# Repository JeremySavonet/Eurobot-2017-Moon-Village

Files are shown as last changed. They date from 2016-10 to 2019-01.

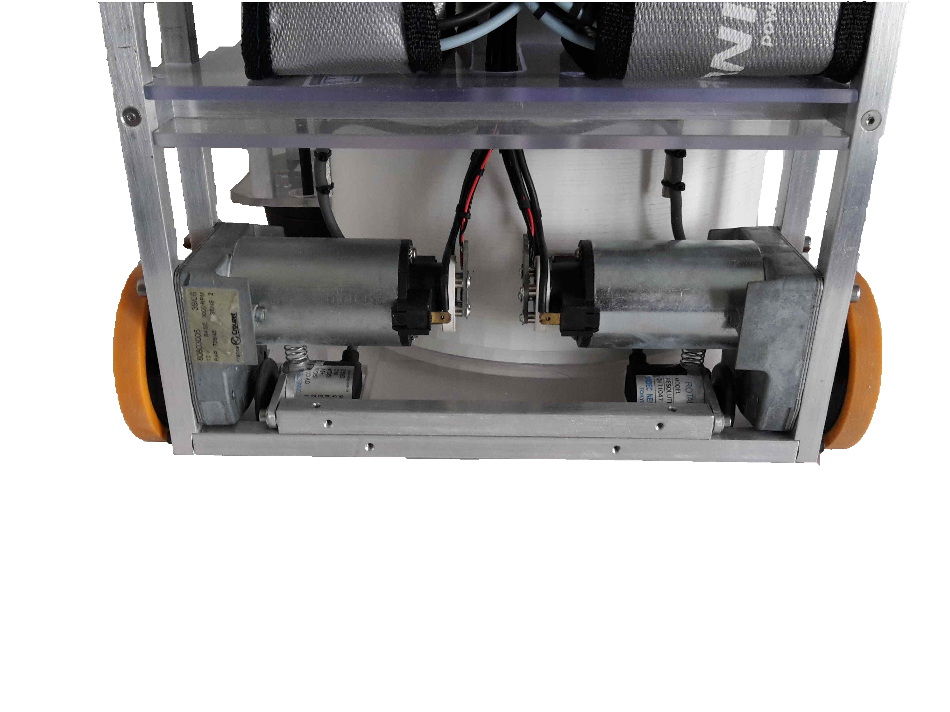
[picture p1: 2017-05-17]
admin/Poster/IMG_20170425_171114.png

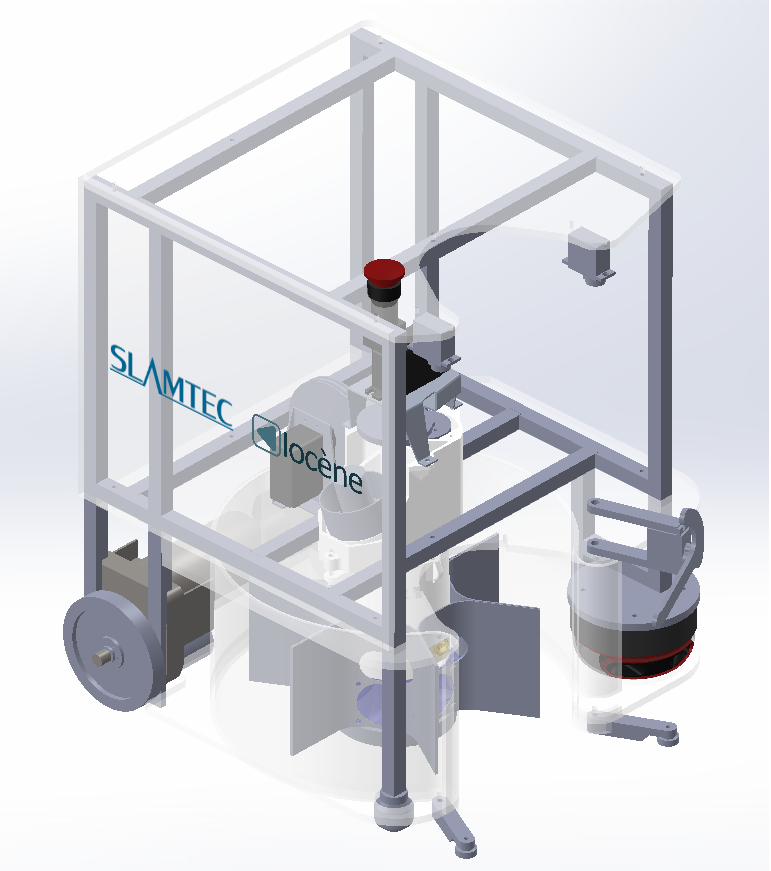
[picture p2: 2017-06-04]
meca/Images/Robot 1.png

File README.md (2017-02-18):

EUROBOT 2017 - Moon Village
====

Make the SD card with the Linux Image:
===

First checkout this repository by using:

```
shell$ git clone git://github.com/ikwzm/FPGA-SoC-Linux
shell$ cd FPGA-SoC-Linux
shell$ git lfs pull origin master
```

Make sure you have git lfs installed before running the third command.
If not installed, just type:
```
### On Debian:

echo 'deb http://http.debian.net/debian wheezy-backports main' > /etc/apt/sources.list.d/wheezy-backports-main.list
curl -s https://packagecloud.io/install/repositories/github/git-lfs/script.deb.sh | sudo bash
sudo apt-get install git-lfs
git lfs install

### On MacOs:
brew install git-lfs
git lfs install
```

When you are done, create the SD card. You will need to create two partition on it:
  * One around 524Mo in FAT format
  * The other around 2,7Go in Ext3 format

You can use the method of your choice to create those partition.
Then, it's time to write data on your SD card:

```
shell# mount /dev/sdc1 /mnt/usb1
shell# mount /dev/sdc2 /mnt/usb2
shell# cp target/de0-nano-soc/boot/* /mnt/usb1
shell# dd if=target/de0-nano-soc/u-boot/u-boot-spl.sfp of=/dev/sdc3 bs=64k seek=0
shell# dd if=target/de0-nano-soc/u-boot/u-boot.img of=/dev/sdc3 bs=64k seek=4
shell# tar xfz debian8-rootfs-vanilla.tgz -C /mnt/usb2
shell# cp fpga-soc-linux-drivers-4.4.7-armv7-fpga_0.0.2-1_armhf.deb /mnt/usb2/home/fpga
shell# umount mnt/usb1
shell# umount mnt/usb2
```

OR,
==

You can run the script robot.sh provided in robot_filesystem folder.

```
sudo ./robot.sh
```

Just provides data when asked (path to a valid rootfs and path to your sd card).

Note:
---
Maybe we can reduce the size of our image. For example:
  * 1Mo: Uboot
  * 256Mo: RBF + others stuffs
  * 256Mo: RootFs

and then use the command:
```
sudo resize2fs /dev/mmcblk0p2

```

to enlarge rootfs partition.

Now, you'r done with the SD card. You have a nice Debian distribution working on the DE0 nano SoC.

Change the RBF
===
You can change the default RBF file that come with the distribution above.
Just create your sof file that fit your needs with Quartus Tools.
Convert the sof file to a rbf file using the command:
```
quartus_cpf -c -o bitstream_compression=on DE0_NANO_SOC.sof DE0_NANO_SOC.rbf
```

Replace the rbf with yours on the first partition of your SD card.

Setup the CrossCompile Toolchain:
====

1- Get Arm Cross Compiler: GCC

Get the latest gcc compiler for ARM:

We will be using the standard Linaro GCC toolchain for the ARMv7 instruction set
to compile our projects.

```
wget -c https://releases.linaro.org/components/toolchain/binaries/6.2-2016.11/arm-linux-gnueabihf/gcc-linaro-6.2.1-2016.11-i686_arm-linux-gnueabihf.tar.xz
tar -xvf gcc-linaro-6.2.1-2016.11-i686_arm-linux-gnueabihf.tar.xz
export CROSS_COMPILE=$PWD/gcc-linaro-6.2.1-2016.11-i686_arm-linux-gnueabihf/bin/arm-linux-gnueabihf-
```

For others gcc version, go to:
https://releases.linaro.org/components/toolchain/binaries/6.2-2016.11/arm-linux-gnueabihf/

Or, simply run:

```
sudo apt-get install gcc-arm-linux-gnueabi
```

2- Get Linux Kernel from sources

Note:
---

We use Kernel 4.5.x

Tested:

  * Kernel sources

```
git clone https://github.com/altera-opensource/linux-socfpga.git
cd linux-socfpga
git tag
git checkout rel_socfpga-4.5_16.06.01_pr
```
  * Configuring the Kernel

```
make CROSS_COMPILE=arm-linux-gnueabi- ARCH=arm socfpga_defconfig
```

Maybe on some system you will need to install extra packages:

```
sudo apt-get install libncurses5-dev

or,

sudo dpkg --add-architecture i386 sudo apt-get update sudo apt-get install libc6:i386 libstdc++6:i386 libfontconfig1:i386 libfreetype6:i386 libice6:i386 lib32ncurses5 zlib1g:i386 libusb-0.1-4:i386
```

After that, Open the Kernel configuration tool:

```
make CROSS_COMPILE=arm-linux-gnueabi- ARCH=arm menuconfig
```

Note:
---

Go into the “General Setup” menu. Uncheck “Automatically append version information to the version string”. This will prevent the kernel from adding extra “version” information to the kernel.

And, enter the “Enable the block layer” menu option and enable the “Support for large (2TB+) block devices and files” option. Although the chances of you actually having 2TB+ files on your filesystem are small, if you look at the help for this option (press “?”) you’ll notice that this option is required to be enabled if you’re using the EXT4 filesystem (which we are). If you forget to enable this option, the kernel will mount your filesystem in read-only mode and print out a helpful message reminding you to come back and enable this if you want full read/write support.

When you’re done looking at the available options, hit the right arrow key to select the “Save” option at the bottom of the window and press enter. When asked for a filename, leave it at the default (“.config”) and hit enter. Hit enter again, then exit the configuration tool.

  * Compiling the Kernel and create zImage

```
make CROSS_COMPILE=arm-linux-gnueabi- ARCH=arm LOCALVERSION= zImage
```

Use the zImage created to make your SD card.

The part below is not tested and is here for information if we decide to try other linux kernel from others sources:
==

```
git clone https://github.com/RobertCNelson/socfpga-kernel-dev
cd socfpga-kernel-dev/

git checkout origin/v4.4.x -b LOCAL-BRANCH-NAME
```

You can checkout other version. For example:

For 4.6.x (Stable)

```
git checkout origin/v4.6.x -b LOCAL-BRANCH-NAME
```

For 4.7.x (Prepatch)

```
git checkout origin/v4.7.x -b LOCAL-BRANCH-NAME
```

3- Build the kernel

```
./build_kernel.sh
```

Wifi with Realtek 8192du driver:
====

There is two options to make the WiFi works on the board:

  * You are not using a 4.5.0 Linux kernel, so you need to build your own
    versionkernel of the kernel module by fetching source of the 8192d and
    compile it with your crosstoolchain.
  * Or, just use the 8192du.ko already built for our kernel (4.5.0).

  Once you have the 8192du.ko in your linux rootFs, you can install the module
  manually (insmod path-to-your-8192du.ko) or at boot time:

In your rc.local file put:
```
insmod 8192du.ko

ifup wlan0
```

If the module is plugged in on your board you can see now a new interface called
wlan0 if you type 'ifconfig' in a shell.

Setup a WiFi Access point:
====

Install the following package:

```
apt-get install dnsmasq hostapd
```

Create an hostapd configuration file in /etc/hostapd/hostapd.conf

```
interface=wlan0
ssid=YOUR-SSID
channel=1
hw_mode=g
wpa=3
wpa_passphrase=YOUR-PASSWORD
wpa_key_mgmt=WPA-PSK
wpa_pairwise=TKIP
rsn_pairwise=CCMP
```

DO NOT forget to edit the file /etc/init.d/hostapd and set:

```
DAEMON_CONF=/etc/hostpad/hostapd.conf
```
Also edit the file /etc/default/hostapd and change the line:

```
DAEMON_CONF=/etc/hostpad/hostapd.conf
```

Then, update your /etc/network/interfaces file with the following:

```
auto wlan0
iface wlan0 inet static
hostapd /etc/hostapd/hostapd.conf
address 192.168.10.1
netmask 255.255.255.0
```

Finally, restart your wlan0 interface by typing:

```
ifdown wlan0
ifup wlan0
```

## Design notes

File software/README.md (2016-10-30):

Software section:
====

Before started:
===
  
  * Get the latest demo Linux Image:
    http://releases.rocketboards.org/release/2015.10/atlas/atlas_sdcard_v1.1.img.tgz

  * Burn the Image to your micro SD card using dd (Linux) or Win32DiskImage
    (Windows)
  
  * Make sure you have connected the UART cable (J13) before powering up the board

  * Put the MSEL jumper like this : ON / OFF / ON / OFF / ON / XX

  * Power the board and log in with root

Required Software:
===

  * SoC EDS from Altera : can be dowloaded here : http://dl.altera.com/soceds/

Test the HelloWorld example program:
===

  * On Windows, start the Embedded command shell from altera
(C:/Altera/Version/Embedded/command_shell.bat)
  
  * Go to the project folder using cd and run make

  * Use SCP to upload the binary on the board

  * Use chmod +x and then run

  * You are done !!!!

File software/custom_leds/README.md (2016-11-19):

HPS_FPGA_CUSTOM_LED:
====

This is a demo program to get started with the DEO nano SoC board and test that your development environment is set up right.

Before started:
===
  * You'll need to install the Altera suite which is composed of:
  - Quartus Prime Edition: http://dl.altera.com/16.1/?edition=lite
  - Quartus SoC EDS: http://dl.altera.com/soceds/

  * Create a Debian Image for the board (see: https://github.com/JeremySavonet/Eurobot-2017-Moon-Village/blob/master/README.md)

  * Burn the Image to your micro SD card

  * Generate the rbf file from the sof file

  * Make sure you have connected the UART cable (J13) before powering up the board

  * Put the MSEL jumper like this : ON / OFF / ON / OFF / ON / XX

  * Power the board
  * Open the UART with scree for example:
<code>screen /dev/ttyUSB0 115200</code>
  * Log in with root when needed (login: root, mdp: admin)

Troubleshooting:
===
  * On Debian Jessie (8), you'll probably need to execute the following commands to end setup the cross compilation toolchains:
<code>
sudo dpkg --add-architecture i386
sudo apt-get update
sudo apt-get install libc6:i386 libstdc++6:i386 libfontconfig1:i386 libfreetype6:i386 libice6:i386 lib32ncurses5 zlib1g:i386 libusb-0.1-4:i386
</code>

Required Software:
===
  * Quartus Prime Edition from Altera: http://dl.altera.com/16.1/?edition=lite
  * SoC EDS from Altera : can be dowloaded here : http://dl.altera.com/soceds/

Note:
===
  * To run generate.sh script and Make, you'll need to start the embedded_command_shell.sh. This script will set up correctly all the environment variable for you. It can be found in the EDS folder. For me: /home/user/intelFPGA/embedded/embedded_command_shell.sh.

Test the HPS_FPGA_CUSTOM_LED example program:
===
  * On Linux/Windows, start the Embedded command shell from altera
  * Go to the fpga folder using cd and file the sof file.
  * Run the following command to generate your rbf file:
```
quartus_cpf -c -o bitstream_compression=on your_sof_file.sof DE0_NANO_SOC.rbf
```
  * Change the rbf file on your SD card
  * Go to the fpga folder using cd and run generate.sh script. It will create the hps_0.h header files to make your program and interact with the FPGA.
  * Go to the software folder using cd and type make. It will create a binary file HPS_FPGA_CUSTOM_LED.
  * You can use SCP or place the binary file directly into your sd card at: /home/fpga/
  * Disconnect your SD card and reboot the board.
  * You should see Linux booting and end to a command prompt.
  * cd to /home/fpga and run the HPS_FPGA_CUSTOM_LED binary
  * You are done !

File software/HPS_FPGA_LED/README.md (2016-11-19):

HPS_FPGA_LED:
====

This is a demo program to get started with the DEO nano SoC board and test that your development environment is set up right.

Before started:
===
  * You'll need to install the Altera suite which is composed of:
  - Quartus Prime Edition: http://dl.altera.com/16.1/?edition=lite
  - Quartus SoC EDS: http://dl.altera.com/soceds/

  * Get the latest demo Linux Image:
    http://releases.rocketboards.org/release/2015.10/atlas/atlas_sdcard_v1.1.img.tgz

  * Burn the Image to your micro SD card using dd (Linux) or Win32DiskImage
    (Windows)

  * Make sure you have connected the UART cable (J13) before powering up the board

  * Put the MSEL jumper like this : ON / OFF / ON / OFF / ON / XX

  * Power the board
  * Open the UART with scree for example:
<code>screen /dev/ttyUSB0 115200</code>
  * Log in with root when needed

Troubleshooting:
===
  * On Debian Jessie (8), you'll probably need to execute the following commands to end setup the cross compilation toolchains:
<code>
sudo dpkg --add-architecture i386
sudo apt-get update
sudo apt-get install libc6:i386 libstdc++6:i386 libfontconfig1:i386 libfreetype6:i386 libice6:i386 lib32ncurses5 zlib1g:i386 libusb-0.1-4:i386
</code>

Required Software:
===
  * Quartus Prime Edition from Altera: http://dl.altera.com/16.1/?edition=lite
  * SoC EDS from Altera : can be dowloaded here : http://dl.altera.com/soceds/

Note:
===
  * To run generate.sh script and Make, you'll need to start the embedded_command_shell.sh. This script will set up correctly all the environment variable for you. It can be found in the EDS folder. For me: /home/user/intelFPGA/embedded/embedded_command_shell.sh.

Test the HPS_FPGA_LED example program:
===
  * On Linux/Windows, start the Embedded command shell from altera
  * Go to the fpga folder using cd and run generate.sh script. It will create the hps_0.h header files to make your program and interact with the FPGA.
  * Go to the software folder using cd and type make. It will create a binary file HPS_FPGA_LED.
  * You can use SCP or place the binary file directly into your sd card at: /home/root/
  * Use chmod +x and then run
  * You will need to program the FPGA to:
  - Start Quartus programmer.
  - Select the hardware and click autodetect.
  - You'll see the SOCVHPS and FPGA.
  - Click on the FPGA and select 'change file'.
  - Go to fpga folder -> output and find the *.sof file
  - Select write and start.
  * You are done !

Note that if you reboot the board, you'll need to program the FPGA again since it's not write in the flash.

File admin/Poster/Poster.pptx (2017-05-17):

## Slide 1

WESTBOT (France )

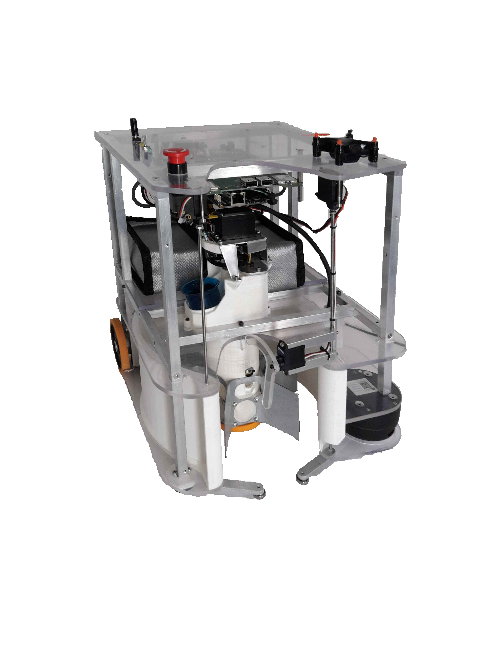
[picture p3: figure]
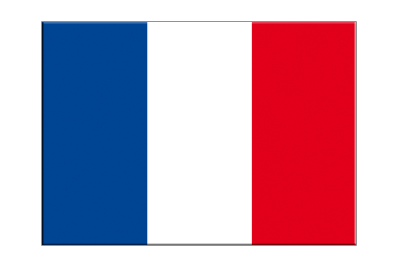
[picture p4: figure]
Autocollant drapeau France, 5 pcs - 7 x 10 cm

Elec : architecture autour d’un cyclone V (FPGA+ARM)

Funny action : quadricoptère

Turbine éjection minerais (et réjection roches)

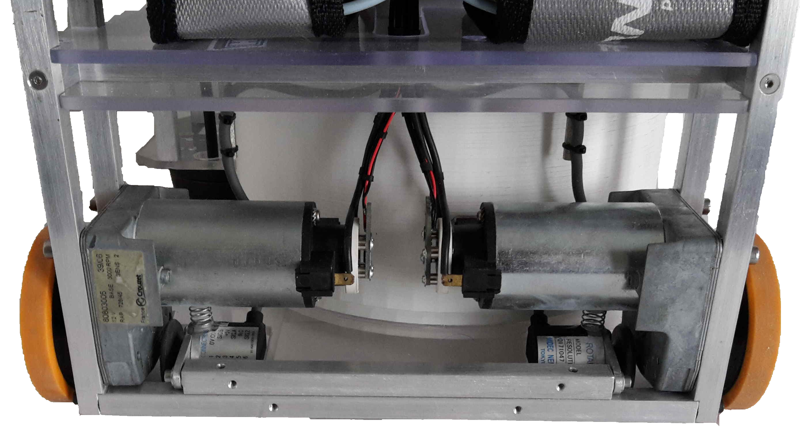
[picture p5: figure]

Bloc moteur + roues codeuses

Doigt de retournement et éjection modules

Télémètre laser 2D

Carrousel stockage modules et minerai

Capteur couleur

Roue orientation couleur module

Team :
- Brice Vincent
- Jérémy Savonet
- Etienne Boilley

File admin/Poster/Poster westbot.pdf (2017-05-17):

# WESTBOT (France )

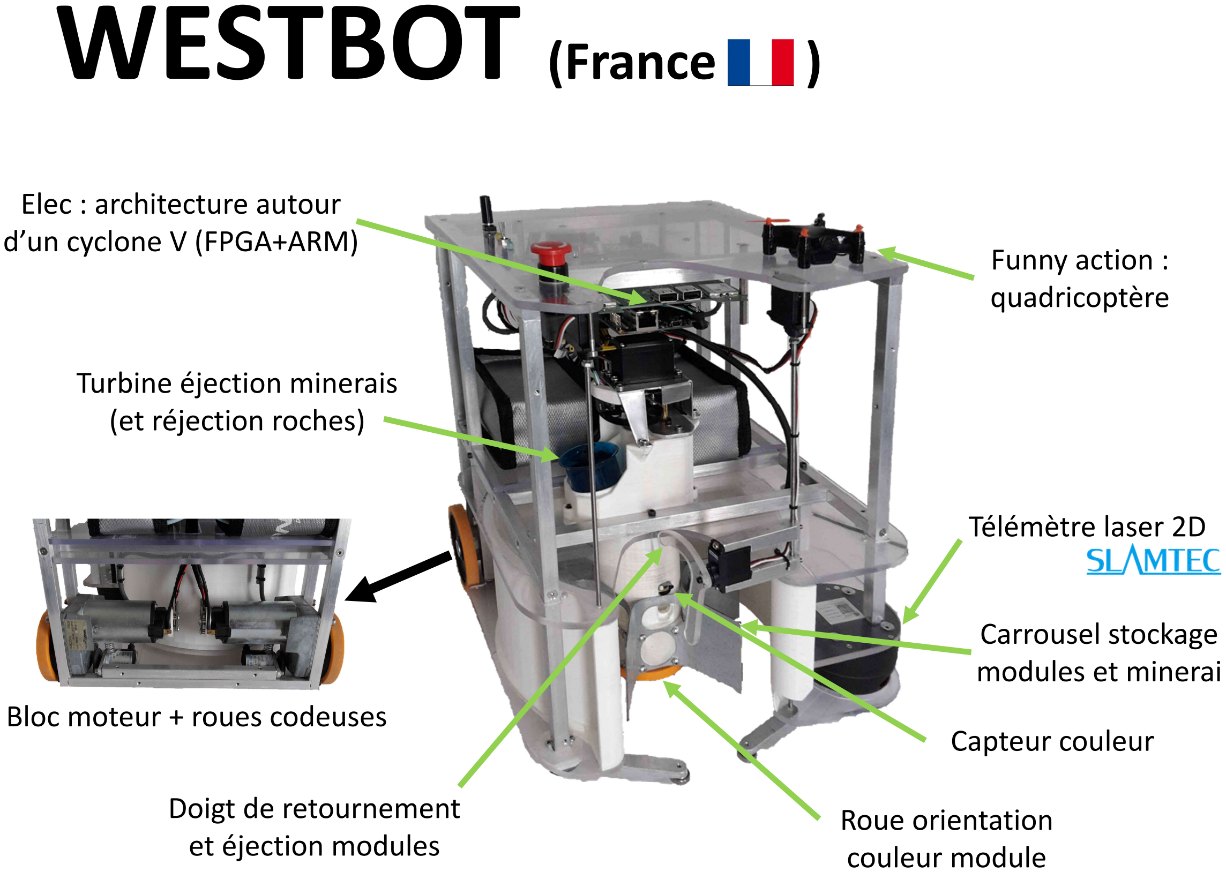
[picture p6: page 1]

Télémètre laser 2D

Carrousel stockage
modules et minerai

Doigt de retournement
et éjection modules

Turbine éjection minerais
(et réjection roches)

Roue orientation
couleur module

Funny action :
quadricoptère

Elec : architecture autour d’un cyclone V (FPGA+ARM)

Capteur couleur

Bloc moteur + roues codeuses

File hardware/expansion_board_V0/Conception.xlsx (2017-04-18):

Actionneur / capteur | Composant d'interface | FPGA pin | FPGA connecteur no | Signal name | Pin function | Fpga IO | AN high speed | AN low speed | 5v fpga | 3v3 sensors | 5v sensors | 12v sensors (LIPO) | A5v servo | A12v motor (LIPO) | 24v motor (LIPO)
M0 - Moteur R | Hbridge 50v 10A |  | 0.28 | M0_PWMA | PWM | 1 |  |  |  |  |  |  |  |  | 10.00
 | DRV8432 |  | 0.32 | M0_PWMB | PWM | 1
 | Current |  | 0.27 | M01_FAULT | INT | 1
Crouzet | INA240 |  | - | M0_CS | AN |  | 1 |  |  |  | 0.002
M1 - Moteur L | Hbridge 50v 10A |  | 0.25 | M1_PWMA | PWM | 1 |  |  |  |  |  |  |  |  | 10.00
 | DRV8432 |  | 0.26 | M1_PWMB | PWM | 1
 | Current |  | 0.24 | M01_RESET | INT | 1
Crouzet | INA240 |  | - | M1_CS | AN |  | 1 |  |  |  | 0.002
QEI0 - Codeur R | Pullup+Isolation |  | 0.14 | QEI0_A | QEI | 1 |  |  |  |  | 0.06
OEZ 1024 2MC |  |  | 0.16 | QEI0_B | QEI | 1
QEI1 - Codeur L |  |  | 1.36 | QEI1_A | QEI | 1 |  |  |  |  | 0.06
OEZ 1024 2MC | TXB0108 |  | 1.38 | QEI1_B | QEI | 1
M2 - Moteur carrousel | Hbridge 12v/50v 5A |  | 1.19 | M2_PWMA | PWM | 1 |  |  |  |  |  |  |  | 3.00 | 0.00
 |  |  | 1.17 | M2_PWMB | PWM | 1
Maxon | DRV8432 |  | 1.23 | M3_PWMA | PWM | 1 |  |  |  |  |  |  |  | 3.00 | 0.00
M3 - Moteur roue carrousel | Current |  | 1.21 | M3_PWMB | PWM | 1
 | INA240 |  | 1.25 | M23454_FAULT | INT | 1
 | Current |  | - | M2_CS | AN |  | 1 |  |  |  | 0.002
MG995 | INA240 |  | - | M3_CS | AN |  | 1 |  |  |  | 0.002
M4 - Moteur | Hbridge 12v/50v 5A |  | 1.31 | M4_PWMA | PWM | 1 |  |  |  |  |  |  |  | 3.00 | 0.00
 |  |  | 1.27 | M4_PWMB | PWM | 1
 |  |  | 1.35 | M5_PWMA | PWM | 1 |  |  |  |  |  |  |  | 3.00 | 0.00
M5 - Moteur (without CS) | DRV8432 |  | 1.33 | M5_PWMB | PWM | 1
 | Current |  | 1.37 | M2345_RESET | INT | 1
 | INA240 |  | - | M5_CS | AN |  | 1
QEI2 - Codeur moteur | Isolation |  | 0.18 | QEI2_A | QEI | 1 |  |  |  |  | 0.02
 |  |  | 0.19 | QEI2_B | QEI | 1
AS5047P |  |  | 0.20 | QEI2_Z | QEI | 1
QEI3 - Codeur moteur |  |  | 1.28 | QEI3_A | QEI | 1 |  |  |  |  | 0.02
 |  |  | 1.32 | QEI3_B | QEI | 1
AS5047P | TXB0108 |  | 1.34 | QEI3_Z | QEI | 1
Turbine | Contrôle moteur+dir |  | A.4 | ESC0_PWM | PWM | 1 |  |  |  |  |  |  | 0.10 | 20.00
 | ESC Turnigy plush 40A
 | Relai V23101-D0103-A201 |  | A.5 | ESC0_DIR | TTL | 1 |  |  |  |  |  |  | 0.08
 | Transistor+diode
Dr. Mad Thrust 40mm 8B 8000kv | Current |  | - | ESC0_CS | AN |  | 1 |  |  |  | 0.002
 | INA240
Turbine | Contrôle moteur+dir |  | A.7 | ESC1_PWM | PWM | 1 |  |  |  |  |  |  | 0.00 | 0.00
 | ESC Turnigy plush 40A
 | Relai V23101-D0103-A201 |  | A.6 | ESC1_DIR | TTL | 1 |  |  |  |  |  |  | 0.08 | 0.10
 | Transistor+diode
Dr. Mad Thrust 40mm 8B 8000kv | Current |  | - | ESC1_CS | AN |  | 1 |  |  |  | 0.002
 | INA240
S0 - Arm R | Isolation |  | 1.15 | S0 | PWM | 1 |  |  |  |  |  |  | 0.50
S1 - bras D |  |  | 1.13 | S1 | PWM | 1 |  |  |  |  |  |  | 0.50
S2 - |  |  | 1.9 | S2 | PWM | 1 |  |  |  |  |  |  | 0.50
S3 - |  |  | 1.7 | S3 | PWM | 1 |  |  |  |  |  |  | 0.50
S4 - |  |  | 0.31 | S4 | PWM | 1 |  |  |  |  |  |  | 0.50
S5 - |  |  | A.0 | S5 | PWM | 1 |  |  |  |  |  |  | 0.50
S6 - ARM L |  |  | A.1 | S6 | PWM | 1 |  |  |  |  |  |  | 0.50
S7 - Dépose | TXB0108 |  | A.2 | S7 | PWM | 1 |  |  |  |  |  |  | 0.50
 | Current |  | - | AN8 | AN |  |  | 1
 |  |  | - | AN9 | AN |  |  | 1
 |  |  | - | AN10 | AN |  |  | 1
 |  |  | - | AN11 | AN |  |  | 1
 |  |  | - | AN12 | AN |  |  | 1
 |  |  | - | AN13 | AN |  |  | 1
 |  |  | - | AN14 | AN |  |  | 1
 |  |  | - | AN15 | AN |  |  | 1
IO0 - Tirette | Isolation |  | 0.17 | IO0 | IO | 1 |  |  |  |  | 0.01
IO1 - Led couleur |  |  | 0.15 | IO1 | IO | 1 |  |  |  |  | 0.01
IO2 - Switch couleur |  |  | 0.13 | IO2 | IO | 1 |  |  |  |  | 0.01
IO3 - Arret d'urgence |  |  | 0.9 | IO3 | IO | 1 |  |  |  |  | 0.01
IO4 - in |  |  | 0.7 | IO4 | IO | 1 |  |  |  |  | 0.01
IO5 - in |  |  | 0.5 | IO5 | IO | 1 |  |  |  |  | 0.01
IO6 - out |  |  | 0.3 | IO6 | IO | 1 |  |  |  |  | 0.01
IO7 - out | TXB0108 |  | 0.1 | IO7 | IO | 1 |  |  |  |  | 0.01
AN0 |  |  | - | AN0 | AN |  |  | 1 |  |  | 0.01
AN1 |  |  | - | AN1 | AN |  |  | 1 |  |  | 0.01
AN2 |  |  | - | AN2 | AN |  |  | 1 |  |  | 0.01
AN3 |  |  | - | AN3 | AN |  |  | 1 |  |  | 0.01
AN4 |  |  | - | AN4 | AN |  |  | 1 |  |  | 0.01
AN5 |  |  | - | AN5 | AN |  |  | 1 |  |  | 0.01
AN6 |  |  | - | AN6 | AN |  |  | 1 |  |  | 0.01
AN7 |  |  | - | AN7 | AN |  |  | 1 |  |  | 0.01
Uart0 | Isolation |  | 0.39 | RX0 | UART | 1 |  |  |  |  | 0.20
 |  |  | 0.40 | TX0 | UART | 1
Uart1 |  |  | 1.4 | RX1 | UART | 1 |  |  |  |  | 0.20
 |  |  | 1.6 | TX1 | UART | 1
Uart2 - Télémètre |  |  | 0.37 | RX2 | UART | 1 |  |  |  |  | 1.00
 |  |  | 0.38 | TX2 | UART | 1
Rplidar A2 |  |  | A.9 | TELEM_PWM | PWM | 1
Uart3 |  |  | 1.8 | RX3 | UART | 1 |  |  |  |  |  | 0.50
 |  |  | 1.10 | TX3 | UART | 1
Balise | TXB0108 |  | A.3 | BALISE | NA | 1
I2C0 - Proximity sensors | Isolation |  | 0.23 | SCL0 | I2C | 1 |  |  |  |  | 0.10
 |  |  | 0.21 | SDA0 | I2C | 1
VL6180x |  |  | 0.22 | I2C0 | TTL | 1
I2C1 - Proximity sensors |  |  | 1.26 | SCL1 | I2C | 1 |  |  |  |  | 0.10
 |  |  | 1.22 | SDA1 | I2C | 1
VL6180x | TXS0108 |  | 1.24 | I2C1 | TTL | 1
SPI0 => QEI | Isolation |  | 0.33 | SCLK0 | SPI | 1 |  |  |  |  | 0.10
 |  |  | 0.35 | MOSI0 | SPI | 1
 |  |  | 0.36 | MISO0 | SPI | 1
 |  |  | 0.34 | SS0 | CS | 1
SPI1 |  |  | 1.14 | SCLK1 | SPI | 1 |  |  |  |  | 0.10
 |  |  | 1.18 | MOSI1 | SPI | 1
 |  |  | 1.20 | MISO1 | SPI | 1
 | TXB0108 |  | 1.16 | SS1 | TTL | 1
IMU |  |  | 1.3 | IMU_SS | TTL | 1
 |  |  | 1.5 | IMU_DRDY | INT | 1
 | MPU9250 |  | A.R | IMU_FSYNC | TTL | 1
ADC
ADC 0 | >16bits >25kHz/voie |  | 0.8 | AD0_SCLK | SPI | 1 | -8 |  |  |  | 0.15
 |  |  | 0.2 | AD0_MISO | SPI | 1
 |  |  | 0.10 | AD0_DRDY | INT | 1
 |  |  | 0.4 | AD0_SYNC | TTL | 1
 | ADS1278 |  | 0.6 | AD0_CLK | CLK | 1
ADC 1 | >14bits >1kHz |  | A.14 | AD1_SCLK | SPI | 1 |  | -16 |  |  | 0.08
 |  |  | A.13 | AD1_MOSI | SPI | 1
 |  |  | A.12 | AD1_MISO | SPI | 1
 |  |  | A.10 | AD1_SS | TTL | 1
 |  |  | A.11 | AD1_DRDY | INT | 1
 | ADS1248 |  | A.15 | AD1_RST | TTL | 1
USB4 - Wifi | Gemicom |  | - |  |  |  |  |  |  | 0.40
USB5 - Wifi | Gemicom |  | - |  |  |  |  |  |  | 0.40
USB2 - |  |  | - |  |  |  |  |  |  |  | 0.30
USB3 - |  |  | - |  |  |  |  |  |  |  | 0.30
~~USB1 - Ethernet~~ |  |  | -
USB | Hub USB |  | - |  | USB créés |  |  |  |  | 0.30
 | LAN9512 |  | - |  | USB consommés
Led
Led A |  |  | 1.1 | LEDA | TTL | 1
Led B |  |  | 1.2 | LEDB | TTL | 1
FPGA board |  |  |  |  |  |  |  |  | 2.00
IO |  |  |  |  |  | -89
~~AN~~ | ~~12bits 500kHz multiplexé~~
USB
Ethernet | Altera Cyclone V
Lipo monitoring
Lipo 1 | SN74LV4052 |  | - | LOW_VOLTAGE | AN |  | 1
Lipo 2 |  |  | 1.40 | LV_MUXA | TTL | 1
Lipo 3 |  |  | 1.39 | LV_MUXB | TTL | 1
Tension servo (A5V)
Alarme | 2n2222+buzzer |  | A.8 | BUZZER | TTL | 1 |  |  |  |  |  |  | 0.10
Alimentation
Alim FPGA | TPS82130 |  |  |  |  |  |  |  | -3.00 |  |  | 1.50
Alim sensors | TPS82130 |  |  |  |  |  |  |  |  | -3.00 |  | 1.50
Alim sensors | TPS82130 |  |  |  |  |  |  |  |  |  | -3.00 | 1.50
Alim servo | PTR08060W |  |  |  |  |  |  |  |  |  |  |  | -6.00 | 3.00
Lipo
Lipo électronique | Lipo 3s 4000mAh 15c |  |  |  |  |  |  |  |  |  |  | -40
Lipo moteur 3s | Lipo 3s 4000mAh 15c |  |  |  |  |  |  |  |  |  |  |  |  | -40
Lipo moteur 12s | 4x Lipo 3s 2200mAh 30c |  |  |  |  |  |  |  |  |  |  |  |  |  | -40
TOTAL (si positif => problème) |  |  |  |  |  | 0 | 0 | 0 | -1 | -1.9 | -0.038 | -35 | -1.64 | -4.9 | -20

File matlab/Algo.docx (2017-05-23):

Erreur de position du robot : T=(XY)

Erreur de rotation du robot = R_θ =(cos(θ), sin(θ)-sin(θ), cos(θ))

Point de la bordure (sur le plan) : (x_(ref) y_(ref) )

Point mesuré (par le télémètre) : (xy)

Si l’on applique l’erreur de rotation et position au point mesuré par le télémètre, on est censé tomber sur la bordure correspondante.

(x_(ref) y_(ref) 1)=(I_d , T0, 1)(R_θ , 00, 1)(xy1)

(x_(ref) y_(ref) 1)=(1, 0, X0, 1, Y0, 0, 1)(cos(θ), sin(θ), 0-sin(θ), cos(θ), 00, 0, 1)(xy1)

(x_(ref) y_(ref) 1)=(cos(θ), sin(θ), X-sin(θ), cos(θ), Y0, 0, 1)(xy1)

(x_(ref) y_(ref) 1)=(x.cos(θ)+y.sin(θ)+1.X+0.Yy.cos(θ)-x.sin(θ)+0.X+1.Y1)

Les bordures sont soit verticales, soit horizontales. Donc seul x_(ref) ou y_(ref) est connu. On utilise la ligne correspondante dans la matrice ci-dessus afin d’identifier X, Y et θ .

Si x_(ref) est connu : x_(ref) =( x, y, 1, 0)A

Si y_(ref) est connu : y_(ref) =( y, -x, 0, 1)A

D’où : A=(cos(θ)sin(θ)XY)=((x_((0)) , y_((0)) , 1, 0x_((1)) , y_((1)) , 1, 0…, …, …, …y_((n)) , -x_((n)) , 0, 1))/((x_(ref(0)) x_(ref(1)) …y_(ref(n)) ))

Update correction

(cos(θ), sin(θ), X-sin(θ), cos(θ), Y0, 0, 1)=(cos(θ_2 ), sin(θ_2 ), X_2 -sin(θ_2 ), cos(θ_2 ), Y_2 0, 0, 1).(cos(θ_1 ), sin(θ_1 ), X_1 -sin(θ_1 ), cos(θ_1 ), Y_1 0, 0, 1)

(cos(θ_2 ).cos(θ_1 )-sin(θ_2 ).sin(θ_1 ), cos(θ_2 ).sin(θ_1 )+sin(θ_2 ).cos(θ_1 ), X_1 .cos(θ_2 )+Y_1 .sin(θ_2 )+X_2 -sin(θ_2 ).cos(θ_1 )-cos(θ_2 ).sin(θ_1 ), -sin(θ_2 ).sin(θ_1 )+cos(θ_2 ).cos(θ_1 ), -X_1 .sin(θ_2 )+Y_1 .cos(θ_2 )+Y_2 0, 0, 1)

(cos(θ_1 +θ_2 ), sin(θ_1 +θ_2 ), X_1 .cos(θ_2 )+Y_1 .sin(θ_2 )+X_2 -sin(θ_1 +θ_2 ), cos(θ_1 +θ_2 ), -X_1 .sin(θ_2 )+Y_1 .cos(θ_2 )+Y_2 0, 0, 1)

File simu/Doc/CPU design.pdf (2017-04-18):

# How to design your own CPU on FPGAs with VHDL

## A Lecture by Dr. Juergen Sauermann

## Copyright (C) 2009, 2010 by Dr. Juergen Sauermann

Note: The figures look pretty bad. I am working on the scaling of the PNG files. In the meantime, plase use the HTML version.

# Table of Contents

i

# Table of Contents

### 6 DATA PATH

### 6.3.5 Temporary Z and T Flags | 57 6.4 Other Functions | 57

### 7 OPCODE DECODER | 61

### 7.1 Inputs of the Opcode Decoder | 61 7.2 Outputs of the Opcode Decoder | 61 7.3 Structure of the Opcode Decoder | 62 7.4 Default Values for the Outputs | 63 7.5 Checklist for the Design of an Opcode | 63 7.6 Opcode Implementations | 63 7.6.1 The NOP instruction | 63

7.6.2 8-bit Monadic Instructions | 63
7.6.3 8-bit Dyadic Instructions, Register/Register | 64
7.6.4 8-bit Dyadic Instructions, Register/Immediate | 66
7.6.5 16-bit Dyadic Instructions | 67

### 7.6.6 Bit Instructions | 67 7.6.7 Multiplication Instructions | 68 7.6.8 Instructions Writing To Memory or I/O | 69 7.6.9 Instructions Reading From Memory or I/O | 69 7.6.10 Jump and Call Instructions | 71 7.6.11 Instructions Not Implemented | 75 7.7 Index of all Instructions | 75

### 8 INPUT/OUTPUT | 79

### 8.1 Interface to the CPU | 79 8.2 CLR Signal | 79 8.3 Connection the FPGA Pins | 79 8.4 I/O Read | 80 8.5 I/O Write | 81 8.6 Interrupts | 82 8.7 The UART | 83 8.7.1 The UART Baud Rate Generator | 83 8.7.2 The UART Transmitter | 84 8.7.3 The UART Receiver | 85

### 9 TOOLCHAIN SETUP | 87

8.1 Functional Simulation | 89 8.2 Timing Simulation and FPGA Configuration | 90 8.3 Downloading and Building the Tools | 90 8.4 Preparing the Memory Content | 95 8.5 Performing the Functional Simulation | 97 8.5.1 Preparing a Testbench | 97 8.5.2 Defining Memory Modules | 98 8.5.3 Creating the testbench executable | 101 8.6 Building the Design | 102 8.6.1 Creating an UCF file | 103 8.6.2 Synthesis and Implementation | 104 8.7 Creating a Programming File | 105 8.8 Configuring the FPGA | 105

ii

# Table of Contents

### 9 TOOLCHAIN SETUP

### 8.8.1 Configuring the FPGA via JTAG Boundary Scan | 105 8.8.2 Flashing PROMs | 105

### 10 LISTING OF alu.vhd | 107

### 11 LISTING OF avr_fpga.vhd | 115

### 12 LISTING OF baudgen.vhd | 119

### 13 LISTING OF common.vhd | 121

### 14 LISTING OF cpu_core.vhd | 125

### 15 LISTING OF data_mem.vhd | 131

### 16 LISTING OF data_path.vhd | 135

### 17 LISTING OF io.vhd | 141

### 18 Listing of opc_deco.vhd | 145

### 19 LISTING OF opc_fetch.vhd | 157

### 20 LISTING OF prog_mem_content.vhd | 161

### 21 LISTING OF prog_mem.vhd | 165

### 22 LISTING OF reg_16.vhd | 171

### 23 LISTING OF register_file.vhd | 173

### 24 LISTING OF segment7.vhd | 181

### 25 LISTING OF status_reg.vhd | 185

### 26 LISTING OF uart_rx.vhd | 187

### 27 LISTING OF uart_tx.vhd | 189

### 28 LISTING OF RAMB4_S4_S4.vhd | 191

### 29 LISTING OF test_tb.vhd | 195

### 30 LISTING OF avr_fpga.ucf | 197

### 31 LISTING OF Makefile | 199

iii

# Table of Contents

### 32 LISTING OF hello.c | 201

### 33 LISTING OF make_mem.cc | 203

### 34 LISTING OF end_conv.cc | 207

iv

# 1 INTRODUCTION AND OVERVIEW

This lecture describes in detail how you can design a CPU (actually an embedded system) in VHDL.

The CPU has an instruction set similar to the instruction set of the popular 8-bit CPUs made by Atmel. The instruction set is described in http://www.atmel.com/dyn/resources/prod_documents/doc0856.pdf. We use an existing CPU so that we can reuse a software tool chain (avr-gcc) for this kind of CPU and focus on the hardware aspects of the design. At the end of the lecture, however, you will be able to design your own CPU with a different instruction set.

We will not implement the full instruction set; only the fraction needed to explain the principles, and to run a simple "Hello world" program (and probably most C programs) will be described.

## 1.1 Prerequisites

Initially you will need two programs:

- ghdl from http://ghdl.free.fr (a free VHDL compiler and simulator) and
- gtkwave from http://gtkwave.sourceforge.net (a free visualization tool for the output of ghdl).

These two programs allow you to design the CPU and simulate its functions.

Later on, you will need a FPGA toolchain for creating FPGA design files and to perform timing simulations. For this lecture we assume that the free Xilinx Webpack tool chain is used (http://www.xilinx.com). The latest version of the Xilinx Webpack provides ISE 11 (as of Nov. 2009) but we used ISE 10.1 because we used an FPGA board providing a good old Spartan 2E FPGA (actually an xc2s300e device) which is no longer supported in ISE 11.

Once the CPU design is finished, you need a C compiler that generates code for the AVR CPU. For downloading avr-gcc, start here:

http://www.avrfreaks.net/wiki/index.php/Documentation:AVR_GCC#AVR-GCC_on_Unix_and_Linux

In order to try out the CPU, you will need some FPGA board and a programming cable. We used a Memec "Spartan-IIE LC Development Kit" board and an Avnet "Parallel Cable 3" for this purpose. These days you will want to use a more recent development environment. When the hardware runs, the final thing to get is a software toolchain, for example avr-gcc for the instruction set and memory layout used in this lecture. Optional, but rather helpful, is eclipse (http://www.eclipse.org) with the AVR plugin.

Another important prerequisite is that the reader is familiar with VHDL to some extent. You do not need to be a VHDL expert in order to follow this lecture, but you should not be a VHDL novice either.
1.2 Other useful links.

A good introduction into VHDL design with open source tools can be found here:

http://www.armadeus.com/wiki/index.php?title=How_to_make_a_VHDL_design_in_Ubuntu/Debian

1

## 1.3 Structure of this Lecture

This lecture is organized as a sequence of lessons. The first lessons will describe the VHDL files of the CPU design in a top-down fashion.

Then follows a lesson on how to compile, simulate and build the design.

Finally there is a listing of all design files with line numbers. Pieces of these design files will be spread over the different lessons and explained there in detail. In the end, all code lines in the appendix should have been explained, with the exception of comments, empty lines and the like. Repetitions such as the structure of VHDL files or different opcodes that are implemented in the same way, will only be described once.

All source files are provided (without line numbers) in a tar file that is stored next to this lecture.

## 1.4 Naming Conventions

In all lessons and in the VHDL source files, the following conventions are used:

VHDL entities and components and VHDL keywords are written in lowercase. Signal names and variables are written in UPPERCASE. Each signal has a prefix according to the following rules:

I_ for inputs of a VHDL entity.
Q_ for outputs of a VHDL entity.
L_ for local signals that are generated by a VHDL construct (e.g. by a signal assignment).
x_ with an uppercase x for signals generated by an instantiated entity.
For every instantiated component we choose an uppercase letter x (other than I, L, or Q). All signals driven by the component then get the prefix Q_ (if the instantiated component drives an output of the entity being defined) or the prefix x_ (if the component drives an internal signal).

Apart from the prefix, we try to keep the name of a signal the same across different VHDL files. Unless the prefix matters, we will use the signal name without its prefix in our descriptions.

Another convention is that we use one VHLD source file for every entity that we define and that the name of the file (less the .vhd extension) matches the entity name.

## 1.5 Directory Structure

Create a directory of your choice. In that directory, mkdir the following sub-directories:

app for building the program that will run on the CPU (i.e. hello.c)
simu for object files generated by ghdl
src for VHDL source files of the CPU and avr_fpga.ucf
test for a VHDL testbench
tools for tools end_conv and make_mem
work working directory for ghdl
Initially the directory should look like this:

### 1 INTRODUCTION AND OVERVIEW

2

# ls -R .

./app:
hello.c

./simu:

./src:
alu.vhd
avr_fpga.ucf
avr_fpga.vhd
baudgen.vhd
common.vhd
COPYING
cpu_core.vhd
data_mem.vhd
data_path.vhd
io.vhd
opc_deco.vhd
opc_fetch.vhd
prog_mem_content.vhd
prog_mem.vhd
reg_16.vhd
register_file.vhd
segment7.vhd
status_reg.vhd
uart_rx.vhd
uart_tx.vhd
uart.vhd

./test:
RAMB4_S4_S4.vhd
test_tb.vhd

./tools:
end_conv.cc
make_mem.cc

./work:

## 1.6 Other Useful Tools

This lecture was prepared with 3 excellent tools:

- vim 7.1.38 for preparing the text of the lecture,
- txt2html (http://txt2html.sourceforge.net/) 2.46 for converting the text into html, and
- dia 0.5 for drawing the figures.

### 1 INTRODUCTION AND OVERVIEW

3

### 1 INTRODUCTION AND OVERVIEW

4

# 2 TOP LEVEL

This lesson defines what we want to create and the top level VHDL file for it.

## 2.1 Design Purpose

We assume that the purpose of the design is to build an FPGA with the following features:

- a CPU similar to the Atmel ATmega8,
- a serial port with a fixed baud rate, and
- an output for a single digit 7-segment display.

It is assumed that a suitable hardware exists.

## 2.2 Top Level Design

A CPU with I/O is a somewhat complicated beast. In order to tame it, we brake it down into smaller and smaller pieces until the pieces become trivial.

The trick is to perform the breakdown at points where the connection between the pieces is weak (meaning that it consists of only a few signals).

The top level of our FPGA design, and a few components around the FPGA, looks like this:

5

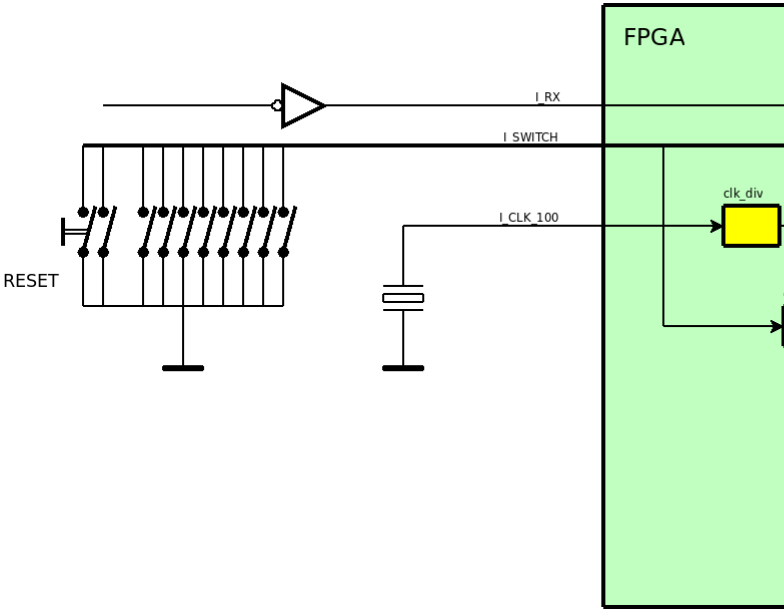
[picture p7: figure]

This design consists of 2 big sub-components cpu and ino, a small sub-component seg, and some local processes like clk_div and deb that are not broken down in other VHDL files, but rather written directly in VHDL.

cpu and ino are described in lessons 4 and 8.

seg is a debug component that has the current program counter (PC) of the CPU as input and displays it as 4 hex digits that show up one by one with a short break between every sequence of hex digits. Since seg is rather board specific, we will not describe it in detail in this lecture.

The local processes are described further down in this lesson. Before that we explain the structure that will be used for all VHDL source file.

### 2 TOP LEVEL

6

## 2.3 General Structure of our VHDL Files

## 2.3.1 Header and Library Declarations

Each VHDL source file starts with a comment containing a copyright notice (all files are released under the GPL) and the purpose of the file. Then follows a declaration of the libraries being used.

## 2.3.2 Entity Declaration

After the header and libraries, the entity that is defined in the VHDL file is declared. We declare one entity per VHDL file. The declaration consists of the name of the entity, the inputs, and the outputs of the entity. In this declaration the order of input and outputs does not matter, but we try to stick to the convention to declare the inputs before the outputs.

There is one exception: the file common.vhd does not define an entity, but a VHDL package. This package contains the definitions of constants that are used in more than one VHDL source file. This ensures that changes to these constants happen in all files using them.

## 2.3.3 Entity Architecture

Finally, the architecture of the entity is specified. The architecture consists of a header and a body.

In the header we declare the components, functions, signals, and constants that are used in the body.

The body defines how the items declared in the header are being used (i.e. instantiated, interconnected etc.). This body contains, so to say, the "intelligence" of the design.

## 2.4 avr_fpga.vhd

The top level of our design is defined in avr_fpga.vhd. Since this is our first VHDL file we explain it completely, line by line. Later on, we will silently skip repetitions of parts that have been described in other files or that are very similar.

## 2.4.1 Header and Library Declarations

avr_fpga.vhd starts with a copyright header.

1 -------------------------------------------------------------------------------2 --
3 -- Copyright (C) 2009, 2010 Dr. Juergen Sauermann
4 --
5 | -- | This code is free software: you can redistribute it and/or modify
6 | -- | it under the terms of the GNU General Public License as published by
7 | -- | the Free Software Foundation, either version 3 of the License, or
8 | -- | (at your option) any later version.
9 --
10 | -- | This code is distributed in the hope that it will be useful,
11 | -- | but WITHOUT ANY WARRANTY; without even the implied warranty of

### 2 TOP LEVEL

7

12 | -- | MERCHANTABILITY or FITNESS FOR A PARTICULAR PURPOSE. | See the
13 | -- | GNU General Public License for more details.
14 --
15 | -- | You should have received a copy of the GNU General Public License
16 | -- | along with this code (see the file named COPYING).
17 | -- | If not, see http://www.gnu.org/licenses/.
18 --
19 -------------------------------------------------------------------------------20 -------------------------------------------------------------------------------21 --
22 | -- Module Name: | avr_fpga - Behavioral
23 | -- Create Date: | 13:51:24 11/07/2009
24 | -- Description: | top level of a CPU
25 --
26 -------------------------------------------------------------------------------27

src/avr_fpga.vhd

The libraries used are more or less the same in all VHDL files:

28 library IEEE;
29 use IEEE.STD_LOGIC_1164.ALL; 30 use IEEE.STD_LOGIC_ARITH.ALL; 31 use IEEE.STD_LOGIC_UNSIGNED.ALL; 32

src/avr_fpga.vhd

The only Xilinx specific components needed for this lecture are the block RAMs. For functional simulation we provide compatible components written in VHDL. For FPGAs from other vendors you can probably include their FPGA libraries, but we have not tested this.

## 2.4.2 Entity Declaration

For a top level entity, the inputs and outputs of the entities are the pins of the FPGA.

For a lower level entity, the inputs and outputs of the entity are associated ("connected") with the inputs and outputs of the instance of the entity in a higher level entity. For this to work, the inputs and outputs of the declaration should match the component declaration in the architecture of another entity that instantiates the entity being declared.

Since we discuss the top-level, our inputs and outputs are pins of the FPGA. The top level entity is declared like this:

### 2 TOP LEVEL

8

### 33 entity avr_fpga is

34 | port ( | I_CLK_100 | : in | std_logic;
35 | | I_SWITCH | : in | std_logic_vector(9 downto 0);
36 | | I_RX | : in | std_logic;
37
38 Q_7_SEGMENT : out std_logic_vector(6 downto 0);
39 | Q_LEDS | : out std_logic_vector(3 downto 0);
40 | Q_TX | : out std_logic);

src/avr_fpga.vhd

We therefore have the following FPGA pins:

Pin | Purpose
I_CLK_100 | a 100 MHz Clock from the board.
I_SWITCH | a 8 bit DIP switch and two single push-buttons.
I_RX | the serial input of our UART.
Q_7_SEGMENT | 7 lines to the LEDs of a 7-segment display.
Q_LEDS | 4 lines to single LEDs
Q_TX | the serial output of our UART.
The lower 8 bits of SWITCH come from a DIP switch while the upper two bits come from two push-buttons. The two push-buttons are used as reset buttons, while the DIP switch goes to the I/O component from where the CPU can read the value set on the switch.

## 2.4.3 Architecture of the Top Level Entity

The architecture has a head and a body, The head starts with the architecture keyword. The body starts with begin and ends with end, like this:

### 43 architecture Behavioral of avr_fpga is

src/avr_fpga.vhd

107 begin

src/avr_fpga.vhd

184 end Behavioral;

src/avr_fpga.vhd

### 2 TOP LEVEL

9

### 2.4.3.1 Architecture Header

As we have seen in the first figure in this lesson, the top level uses 3 components: cpu, io, and seg. These components have to be declared in the header of the architecture. The architecture contains component declarations, signal declarations and others. We normally declare components and signals in the following order:

- declaration of functions
- declaration of constants
- declaration of the first component (type)
- declaration of signals driven by (an instance of) the first component
- declaration of the second component (type)
- declaration of signals driven by (an instance of) the second component
- declaration of signals driven by local processes and the like.

The first component declaration cpu_core and the signals driven by its instances are:

### 45 component cpu_core

46 | port ( | I_CLK | : in | std_logic;
47 | | I_CLR | : in | std_logic;
48 | | I_INTVEC | : in | std_logic_vector( 5 downto 0);
49 | | I_DIN | : in | std_logic_vector( 7 downto 0);
50
51 | Q_OPC | : out std_logic_vector(15 downto 0);
52 | Q_PC | : out std_logic_vector(15 downto 0);
53 | Q_DOUT | : out std_logic_vector( 7 downto 0);
54 | Q_ADR_IO | : out std_logic_vector( 7 downto 0);
55 | Q_RD_IO | : out std_logic;
56 | Q_WE_IO | : out std_logic);
57 end component;
58
59 | signal | C_PC | : std_logic_vector(15 downto 0);
60 | signal | C_OPC | : std_logic_vector(15 downto 0);
61 | signal | C_ADR_IO | : std_logic_vector( 7 downto 0);
62 | signal | C_DOUT | : std_logic_vector( 7 downto 0);
63 | signal | C_RD_IO | : std_logic;
64 | signal | C_WE_IO | : std_logic;

src/avr_fpga.vhd

The second component declaration io and its signals are:

### 66 component io

67 | port ( | I_CLK | : in | std_logic;
68 | | I_CLR | : in | std_logic;
69 | | I_ADR_IO | : in | std_logic_vector( 7 downto 0);
70 | | I_DIN | : in | std_logic_vector( 7 downto 0);

### 2 TOP LEVEL

10

71 | I_RD_IO | : in | std_logic;
72 | I_WE_IO | : in | std_logic;
73 | I_SWITCH | : in | std_logic_vector( 7 downto 0);
74 | I_RX | : in | std_logic;
75
76 Q_7_SEGMENT : out std_logic_vector( 6 downto 0);
77 | Q_DOUT | : out std_logic_vector( 7 downto 0);
78 | Q_INTVEC | : out std_logic_vector(5 downto 0);
79 | Q_LEDS | : out std_logic_vector( 1 downto 0);
80 | Q_TX | : out std_logic);
81 end component;
82
83 | signal N_INTVEC | : std_logic_vector( 5 downto 0);
84 | signal N_DOUT | : std_logic_vector( 7 downto 0);
85 | signal N_TX | : std_logic;
86 | signal N_7_SEGMENT | : std_logic_vector( 6 downto 0);

src/avr_fpga.vhd

Note: Normally we would have used I_ as a prefix for signals driven by instance ino of io. This conflicts, however, with the prefix reserved for inputs and we have used the next letter n of ino as prefix instead.

The last component is seg:

### 88 component segment7

89 | port ( I_CLK | : in | std_logic;
90
91 | I_CLR | : in | std_logic;
92 | I_OPC | : in | std_logic_vector(15 downto 0);
93 | I_PC | : in | std_logic_vector(15 downto 0);
94
95 | Q_7_SEGMENT | : out std_logic_vector( 6 downto 0));
96 end component;
97
98 | signal S_7_SEGMENT | : std_logic_vector( 6 downto 0);

src/avr_fpga.vhd

The local signals, which are not driven by any component, but by local processes and inputs of the entity, are:

100 | signal L_CLK | : std_logic := '0';
101 | signal L_CLK_CNT | : std_logic_vector( 2 downto 0) := "000";
102 | signal L_CLR | : std_logic; | -- reset, | active low
103 | signal L_CLR_N | : std_logic := '0'; | -- reset, | active low
104 | signal L_C1_N | : std_logic := '0'; | -- switch debounce, active low
105 | signal L_C2_N | : std_logic := '0'; | -- switch debounce, active low
106
107 begin

### 2 TOP LEVEL

11

src/avr_fpga.vhd

The begin keyword in the last line marks the end of the header of the architecture and the start of its body.

### 2.4.3.2 Architecture Body

We normally use the following order in the architecture body:

- components instantiated
- processes
- local signal assignments

Thus the architecture body is more or less using the same order as the architecture header. The component instantiations instantiate one or more instances of a component type and connect the "ports" of the instantiated component to the signals in the architecture.

The first component declared was cpu so we also instantiate it first:

109 cpu : cpu_core
110 | port map( | I_CLK | => L_CLK,
111 | | I_CLR | => L_CLR,
112 | | I_DIN | => N_DOUT,
113 | | I_INTVEC | => N_INTVEC,
114
115 | | Q_ADR_IO | => C_ADR_IO,
116 | | Q_DOUT | => C_DOUT,
117 | | Q_OPC | => C_OPC,
118 | | Q_PC | => C_PC,
119 | | Q_RD_IO | => C_RD_IO,
120 | | Q_WE_IO | => C_WE_IO);

src/avr_fpga.vhd

The first line instantiates a component of type cpu_core and calls the instance cpu. The following lines map the names of the ports in the component declaration (in the architecture header) to either inputs of the entity, outputs of the entity, or signals declared in the architecture header.

We take cpu as an opportunity to explain our naming convention for signals. Our rule for entity inputs and outputs has the consequence that all left sides of the port map have either an I_ prefix or an O_ prefix. This follows from the fact that a component instantiated in one architecture corresponds to an entity declared in some other VHDL file and there the I_ or O_ convention applies,

The next observation is that all component outputs either drive an entity output or a local signal that starts with the letter chosen for the instantiated component. This is the C_ in the cpu case. The cpu does not drive an entity output directly (so all outputs map to C_ signals), but in the io outputs there is one driving an entity output (see below).

### 2 TOP LEVEL

12

Finally the component inputs can be driven from more or less anywhere, but from the prefix (L_ or not) we can see if the signal is directly driven by another component (when the prefix is not L_) or by some logic defined further down in the architecture (signal assignments, processes).

Thus for the cpu component we can already tell that this component drives a number of local signals (that are not entity outputs but inputs to other components or local processes)> These signals are those on the right side of the port map starting with C_. We can also tell that there are some local processes generating a clock signal L_CLK and a reset signal L_CLR, and the ino component (which uses prefix N_) drives an interrupt vector N_INTVEC and a data bus N_DOUT.

The next two components being instantiated are ino of type io and seg of type segment7:

122 ino : io
123 | port map( | I_CLK | => L_CLK,
124 | | I_CLR | => L_CLR,
125 | | I_ADR_IO | => C_ADR_IO,
126 | | I_DIN | => C_DOUT,
127 | | I_RD_IO | => C_RD_IO,
128 | | I_RX | => I_RX,
129 | | I_SWITCH | => I_SWITCH(7 downto 0),
130 | | I_WE_IO | => C_WE_IO,
131
132 Q_7_SEGMENT => N_7_SEGMENT,
133 | | Q_DOUT | => N_DOUT,
134 | | Q_INTVEC | => N_INTVEC,
135 | | Q_LEDS | => Q_LEDS(1 downto 0),
136 | | Q_TX | => N_TX);
137
138 seg : segment7
139 | port map( | I_CLK | => L_CLK,
140 | | I_CLR | => L_CLR,
141 | | I_OPC | => C_OPC,
142 | | I_PC | => C_PC,
143
144 Q_7_SEGMENT => S_7_SEGMENT);

src/avr_fpga.vhd

Then come the local processes. The first process divides the 100 MHz input clock from the board into a 25 MHz clock used by the CPU. The design can, with some tuning of the timing optimizations, run at 33 MHz, but for our purposes we are happy with 25 MHz.

148 clk_div : process(I_CLK_100)
149 begin
150 if (rising_edge(I_CLK_100)) then
151 | L_CLK_CNT | <= L_CLK_CNT + "001";
152 if (L_CLK_CNT = "001") then
153 | L_CLK_CNT | <= "000";
154 | L_CLK | <= not L_CLK;

### 2 TOP LEVEL

13

155 end if;
156 end if;
157 end process;

src/avr_fpga.vhd

The second process is deb. It debounces the push-buttons used to reset the cpu and ino components. When either button is pushed ('0' on SWITCH(8) or SWITCH(9)) then CLR_N goes low immediately and stays low for two more cycles after the button was released.

161 deb : process(L_CLK)
162 begin
163 if (rising_edge(L_CLK)) then
164 -- switch debounce
165 | if ((I_SWITCH(8) = '0') or (I_SWITCH(9) = '0')) then | -- pushed
166 | L_CLR_N | <= '0';
167 | L_C2_N | <= '0';
168 | L_C1_N | <= '0';
169 | else | -- released
170 | L_CLR_N | <= L_C2_N;
171 | L_C2_N | <= L_C1_N;
172 | L_C1_N | <= '1';
173 end if;
174 end if;
175 end process;

src/avr_fpga.vhd

Finally we have the signals driven directly from other signals. This kind of signal assignments are the same as processes, but use a simpler syntax for frequently used logic.

177 | L_CLR | <= not L_CLR_N;
178
179 | Q_LEDS(2) | <= I_RX;
180 | Q_LEDS(3) | <= N_TX;
181 | Q_7_SEGMENT | <= N_7_SEGMENT when (I_SWITCH(7) = '1') else S_7_SEGMENT;
182 | Q_TX | <= N_TX;

src/avr_fpga.vhd

CLR is generated by inverting CLR_N. The serial input and the serial output are visualized by means of two LEDs. The 7 segment output can be driven from two sources: from a software controlled I/O register in the I/O unit, or from the seven segment component (that shows the current PC and opcode) being executed. The latter component is quite useful for debugging purposes.

### 2 TOP LEVEL

14

Note: We use a _N suffix to denote an active low signal. Active low signals normally come from some FPGA pin since inside the FPGA active low signals have no advantage over active high signals. In the good old TTL days active low signals were preferred for strobe signals since the HIGH to LOW transition in TTL was faster than the LOW to high transition. Some active low signals we see today are left-overs from those days. Another common case is switches and push-buttons that are held high with a pull-up resistor when open and short-cut to ground when the switch is closed.

## 2.5 Component Tree

The following figure shows the breakdown of almost all components in our design. Only the memory modules in sram and pmem and the individual registers in regs are hidden because they would blow up the structure without providing too much information.

We have already discussed the top level fpga and its 3 components cpu, ino, and seg.

The cpu will be further broken down into a data path dpath, an opcode decode odec, and an opcode fetch opcf. The data path consist of a 16-bit ALU alui, a register file regs, and a data memory sram. The opcode fetch contains a program counter pcnt and a program memory pmem.

The ino contains a uart that is further broken down into a baud rate generator baud, a serial receiver rx, and a serial transmitter tx.

### 2 TOP LEVEL

15

### 2 TOP LEVEL

16

# 3 DIGRESSION: PIPELINING

In this short lesson we will give a brief overview of a design technique known as pipelining. Most readers will already be familiar with it; those readers should take a day off or proceed to the next lesson.

Assume we have a piece of combinational logic that happens to have a long propagation delay even in its fastest implementation. The long delay is then caused by the slowest path through the logic, which will run through either many fast elements (like gates) or a number of slower elements (likes adders or multipliers), or both.

That is the situation where you should use pipelining. We will explain it by an example. Consider the circuit shown in the following figure.

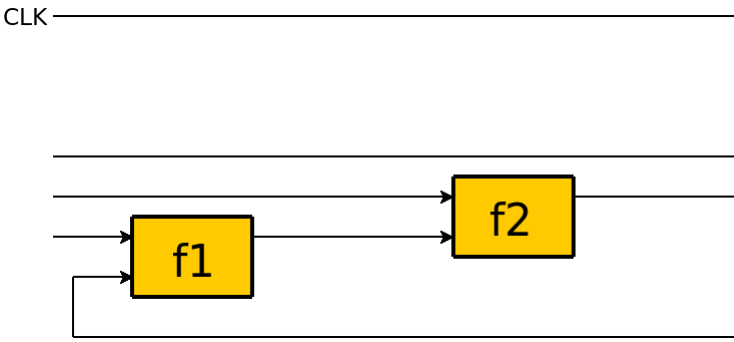
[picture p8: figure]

The circuit is a sequential logic which consists of 3 combinational functions f1, f2, and f3 and a flip-flop at the output of f3.

Let t1, t2, and t3 be the respective propagation delays of f1, f2, and f3. Assume that the slowest path of the combinational logic runs from the upper input of f1 towards the output of f3. Then the total delay of the combinational is t = t1 + t2 + t3. The entire circuit cannot be clocked faster than with frequency 1/t.

Now pipelining is a technique that slightly increases the delay of a combinational circuit, but thereby allows different parts of the logic at the same time. The slight increase in total propagation delay is more than compensated by a much higher throughput.

Pipelining divides a complex combinational logic with an accordingly long delay into a number of stages and places flip-flops between the stages as shown in the next figure.

17

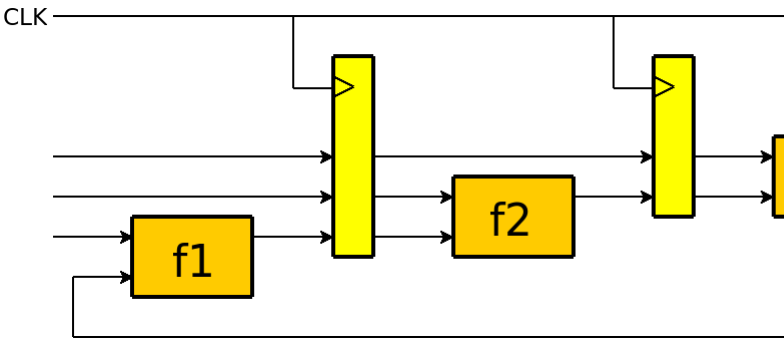
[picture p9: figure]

The slowest path is now max(t1, t2, t3) and the new circuit can be clocked with frequency 1/max(t1, t2, t3) instead of 1/(t1 + t2 + t3). If the functions f1, f2, and f3 had equal propagation delays, then the max. frequency of the new circuit would have tripled compared to the old circuit.

It is generally a good idea when using pipelining to divide the combinational logic that shall be pipelined into pieces with similar delay. Another aspect is to divide the combinational logic at places where the number of connections between the pieces is small since this reduces the number of flip-flops that are being inserted.

The first design of the CPU described in this lecture had the opcode decoding logic (which is combinational) and the data path logic combined. That design had a worst path delay of over 50 ns (and hence a max. frequency of less than 20 MHz). After splitting of the opcode decoder, the worst path delay was below 30 ns which allows for a frequency of 33 MHz. We could have divides the pipeline into even more stages (and thereby increasing the max. frequency even further). This would, however, have obscured the design so we did not do it.

The reason for the improved throughput is that the different stages of a pipeline work in parallel while without pipelining the entire logic would be occupied by a single operation. In a pipeline the single operation is often displayed like this (one color = one operation).

### 3 DIGRESSION: PIPELINING

18

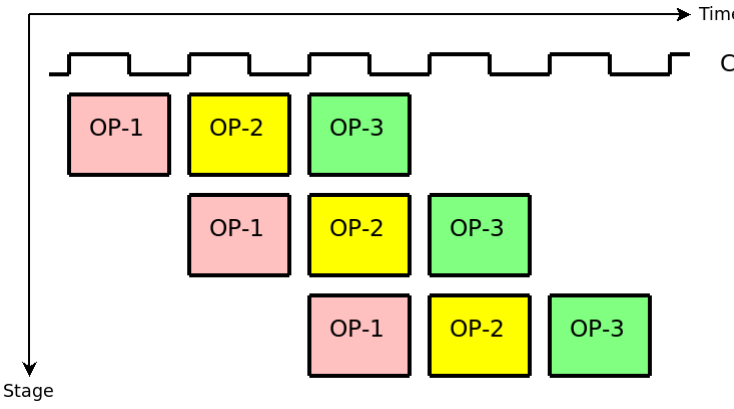
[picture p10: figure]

This kind of diagram shows how an operation is distributed over the different stages over time.

To summarize, pipelining typically results in:

- a slightly more complex design,
- a moderately longer total delay, and
- a considerable improvement in throughput.

### 3 DIGRESSION: PIPELINING

19

### 3 DIGRESSION: PIPELINING

20

# 4 THE CPU CORE

In this lesson we will discuss the core of the CPU. These days, the same kind of CPU can come in different flavors that differ in the clock frequency that that support, bus sizes, the size of internal caches and memories and the capabilities of the I/O ports they provide. We call the common part of these different CPUs the CPU core. The CPU core is primarily characterized by the instruction set that it provides. One could also say that the CPU core is the implementation of a given instruction set.

The details of the instruction set will only be visible at the next lower level of the design. At the current level different CPUs (with different instruction sets) will still look the same because they all use the same structure. Only some control signals will be different for different CPUs.

We will use the so-called Harvard architecture because it fits better to FPGAs with internal memory modules. Harvard architecture means that the program memory and the data memory of the CPU are different. This gives us more flexibility and some instructions (for example CALL, which involves storing the current program counter in memory while changing the program counter and fetching the next instruction) can be executed in parallel).

Different CPU cores differ in the in the instruction set that they support. The types of CPU instructions (like arithmetic instructions, move instructions, branch instructions, etc.) are essentially the same for all CPUs. The differences are in the details like the encoding of the instructions, operand sizes, number of registers addressable, and the like).

Since all CPUs are rather similar apart from details, within the same base architecture (Harvard vs. von Neumann), the same structure can be used even for different instruction sets. This is because the same cycle is repeated again and again for the different instructions of a program. This cycle consists of 3 phases:

- Opcode fetch
- Opcode decoding
- Execution

Opcode fetch means that for a given value of the program counter PC, the instruction (opcode) stored at location PC is read from the program memory and that the PC is advanced to the next instruction.

Opcode decoding computes a number of control signals that will be needed in the execution phase.

Execution then executes the opcode which means that a small number of registers or memory locations is read and/or written.

In theory these 3 phases could be implemented in a combinational way (a static program memory, an opcode decoder at the output of the program memory and an execution module at the output of the opcode decoder). We will see later, however, that each phase has a considerable complexity and we therefore use a 3 stage pipeline instead.

In the following figure we see how a sequence of three opcodes ADD, MOV, and JMP is executed in the pipeline.

21

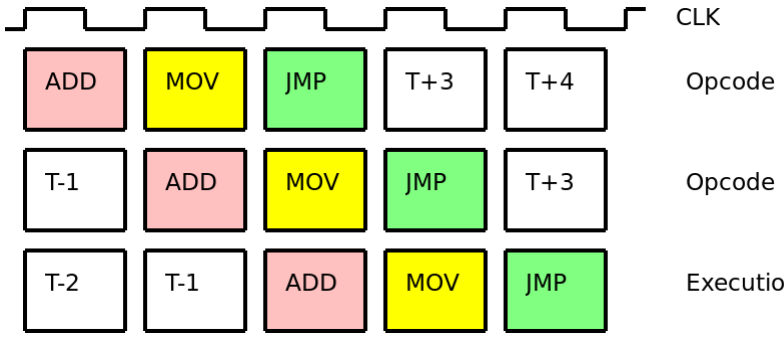
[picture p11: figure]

From the discussion above we can already predict the big picture of the CPU core. It consists of a pipeline with 3 stages opcode fetch, opcode decoder, and execution (which is called data path in the design because the operations required by the execution more or less imply the structure of the data paths in the execution stage:

### 4 THE CPU CORE

22

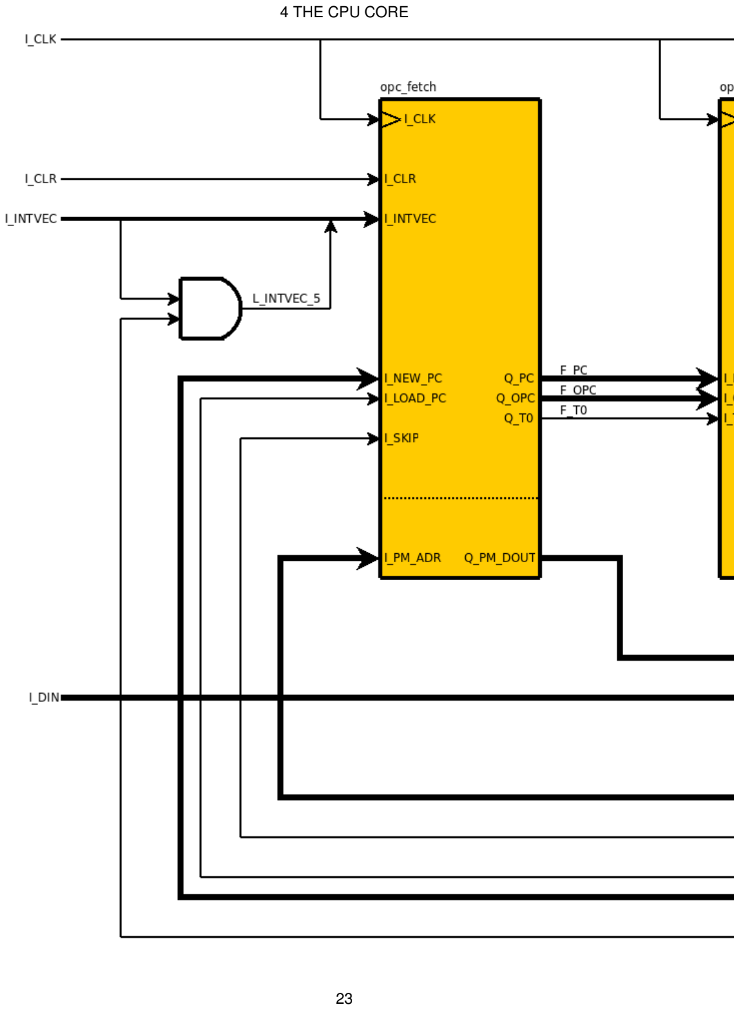
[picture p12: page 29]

### 4 THE CPU CORE

23

The pipeline consists of the opc_fetch stage that drives PC, OPC, and T0 signals to the opcode decoder stage. The opc_deco stage decodes the OPC signal and generates a number of control signals towards the execution stage, The execution stage then executes the decoded instruction.

The control signals towards the execution stage can be divided into 3 groups:

Select signals (ALU_OP, AMOD, BIT, DDDDD, IMM, OPC, PMS, RD_M, RRRRR, and RSEL). These signals control details (like register numbers) of the instruction being executed.

1.

Branch and timing signals (PC, PC_OP, WAIT, (and SKIP in the reverse direction)). These signals control changes in the normal execution flow.

2.

Write enable signals (WE_01, WE_D, WE_F, WE_M, and WE_XYZS). These signals define if and when registers and memory locations are updated.

3.

We come to the VHDL code for the CPU core. The entity declaration must match the instantiation in the top-level design. Therefore:

### 33 entity cpu_core is

34 | port ( | I_CLK | : in | std_logic;
35 | | I_CLR | : in | std_logic;
36 | | I_INTVEC | : in | std_logic_vector( 5 downto 0);
37 | | I_DIN | : in | std_logic_vector( 7 downto 0);
38
39 | Q_OPC | : out std_logic_vector(15 downto 0);
40 | Q_PC | : out std_logic_vector(15 downto 0);
41 | Q_DOUT | : out std_logic_vector( 7 downto 0);
42 | Q_ADR_IO | : out std_logic_vector( 7 downto 0);
43 | Q_RD_IO | : out std_logic;
44 | Q_WE_IO | : out std_logic);

src/cpu_core.vhd

The declaration and instantiation of opc_fetch, opc_deco, and dpath simply reflects what is shown in the previous figure.

The multiplexer driving DIN selects between data from the I/O input and data from the program memory. This is controlled by signal PMS (program memory select):

240 | L_DIN | <= F_PM_DOUT when (D_PMS = '1') else I_DIN(7 downto 0);

src/cpu_core.vhd

### 4 THE CPU CORE

24

The interrupt vector input INTVEC is and'ed with the global interrupt enable bit in the status register (which is contained in the data path):

241 | L_INTVEC_5 | <= I_INTVEC(5) and R_INT_ENA;

src/cpu_core.vhd

This concludes the discussion of the CPU core and we will proceed with the different stages of the pipeline. Rather than following the natural order (opcode fetch, opcode decoder, execution), however, we will describe the opcode decoder last. The reason is that the opcode decoder is a consequence of the design of the execution stage. Once the execution stage is understood, the opcode decoder will become obvious (though still complex).

### 4 THE CPU CORE

25

### 4 THE CPU CORE

26

# 5 OPCODE FETCH

In this lesson we will design the opcode fetch stage of the CPU core. The opcode fetch stage is the simplest stage in the pipeline. It is the stage that put life into the CPU core by generating a sequence of opcodes that are then decoded and executed. The opcode fetch stage is sometimes called the sequencer of the CPU.

Since we use the Harvard architecture with separate program and data memories, we can simply instantiate the program memory in the opcode fetch stage. If you need more memory than your FPGA provides internally, then you can design address and data buses towards an external memory instead (or in addition). Most current FPGAs provide a lot of internal memory, so we can keep things simple.

The opcode fetch stage contains a sub-component pmem, which is is the program memory. The main purpose of the opcode fetch stage is to manipulate the program counter (PC) and to produce opcodes. The PC is a local signal:

69 | signal L_PC | : std_logic_vector(15 downto 0);

src/opc_fetch.vhd

The PC is updated on every clock with its next value. The T0 output is cleared when the WAIT signal is raised. This causes the T0 output to be '1' on the first cycle of a 2 cycle instruction and '0' on the second cycle:

### 86 lpc: process(I_CLK) 87 begin 88 if (rising_edge(I_CLK)) then

89 | L_PC | <= L_NEXT_PC;
90 | L_T0 | <= not L_WAIT;
91 end if;
92 end process;

src/opc_fetch.vhd

The next value of the PC depends on the CLR, WAIT, LOAD_PC, and LONG_OP signals:

94 | L_NEXT_PC | <= X"0000" | when (I_CLR | = '1')
95 | else L_PC | when (L_WAIT | = '1')
96 | else I_NEW_PC | when (I_LOAD_PC = '1')

### 97 else L_PC + X"0002" when (L_LONG_OP = '1')

98 else L_PC + X"0001";

27

src/opc_fetch.vhd

The CLR signal, which overrides all others, resets the PC to 0. It is generated at power on and when the reset input of the CPU is asserted. The WAIT signal freezes the PC at its current value. It is used when an instruction needs two CLK cycles to complete. The LOAD_PC signal causes the PC to be loaded with the value on the NEW_PC input. The LOAD_PC signal is driven by the execution stage when a jump instruction is executed. If neither CLR, WAIT, or LOAD_PC is present then the PC is advanced to the next instruction. If the current instruction is one of JMP, CALL, LDS and STS, then it has a length of two 16-bit words and LONG_OP is set. This causes the PC to be incremented by 2 rather than by the normal instruction length of 1:

100 -- Two word opcodes:
101 --
102 | -- | 9 | 3210
103 -- 1001 000d dddd 0000 kkkk kkkk kkkk kkkk - LDS 104 -- 1001 001d dddd 0000 kkkk kkkk kkkk kkkk - SDS 105 -- 1001 010k kkkk 110k kkkk kkkk kkkk kkkk - JMP
106 -- 1001 010k kkkk 111k kkkk kkkk kkkk kkkk - CALL
107 --
108 | L_LONG_OP | <= '1' when (((P_OPC(15 downto | 9) = "1001010") and
109 | (P_OPC( 3 downto | 2) = "11")) | -- JMP, CALL
110 | or | ((P_OPC(15 downto 10) = "100100") and
111 | (P_OPC( 3 downto | 0) = "0000"))) | -- LDS, STS
112 else '0';

src/opc_fetch.vhd

The CLR, SKIP, and I_INTVEC inputs are used to force a NOP (no operation) opcode or an "interrupt opcode" onto the output of the opcode fetch stage. An interrupt opcode is an opcode that does not belong to the normal instruction set of the CPU (and is therefore not generated by assemblers or compilers), but is used internally to trigger interrupt processing (pushing of the PC, clearing the interrupt enable flag, and jumping to specific locations) further down in the pipeline.

133 | L_INVALIDATE | <= I_CLR or I_SKIP;
134
135 | Q_OPC | <= X"00000000" when (L_INVALIDATE = '1')
136 | else P_OPC | when (I_INTVEC(5) = '0')
137 | else (X"000000" & "00" & I_INTVEC); | -- "interrupt opcode"

src/opc_fetch.vhd

CLR is derived from the reset input and also resets the program counter. SKIP comes from the execution stage and is used to invalidate parts of the pipeline, for example when a decision was made to take a

### 5 OPCODE FETCH

28 conditional branch. This will be explained in more detail in the lesson about branching.

## 5.1 Program Memory

The program memory is declared as follows:

### 36 entity prog_mem is

37 | port ( | I_CLK | : in | std_logic;
38
39 | | I_WAIT | : in | std_logic;
40 | | I_PC | : in | std_logic_vector(15 downto 0); -- word address
41 | | I_PM_ADR | : in | std_logic_vector(11 downto 0); -- byte address
42
43 | Q_OPC | : out std_logic_vector(31 downto 0);
44 | Q_PC | : out std_logic_vector(15 downto 0);
45 | Q_PM_DOUT | : out std_logic_vector( 7 downto 0));
46 end prog_mem;

src/prog_mem.vhd

## 5.2.1 Dual Port Memory

The program memory is a dual port memory. This means that two different memory locations can be read or written at the same time. We don't write to the program memory, be we would like to read two addresses at the same time. The reason are the LPM (load program memory) instructions. These instructions read from the program memory while the program memory is fetching the next instructions. In a way these instructions violate the Harvard architecture, but on the other hand they are extremely useful for string constants in C. Rather than initializing the (typically smaller) data memory with these constants, one can leave them in program memory and access them using LPM instructions,

Without a dual port memory, we would have needed to stop the pipeline during the execution of LPM instructions. Use of dual port memory avoids this additional complexity.

The second port used for LPM instructions consists of the address input PM_ADR and the data output PM_DOUT. PM_ADR is a 12-bit byte address (and consequently PM_DOUT is an 8-bit output. In contrast, the other port uses an 11-bit word address.

The other signals of the program memory belong to the first port which is used for opcode fetches.

## 5.2.2 Look-ahead for two word instructions

The vast majority of AVR instructions are single-word (16-bit) instructions. There are 4 exceptions, which are CALL, JMP, LDS, and STS. These instructions have addresses (the target address for CALL and JMP and data memory address for $LDS# and STS) in the word following the opcode.

There are two ways to handle such opcodes. One way is to look back in the pipeline when the second word is needed. When one of these instructions reaches the execution stage, then the next word is clocked into the

### 5 OPCODE FETCH

29 decoding stage (so we could fetch it from there). It might lead to complications, however, when it comes to invalidating the pipeline, insertion of interrupts and the like.

The other way, and the one we choose, is to divide the program memory into an even memory and an odd memory. The internal memory modules in an FPGA are anyhow small and therefore using two memories is almost as simple as using one (both would consist of a number of smaller modules).

There are two cases to consider: (1) an even PC (shown on the left of the following figure) and (2) an odd PC shown on the right. In both cases do we want the (combined) memory at address PC to be stored in the lower word of the OPC output and the next word (at PC+1) in the upper word of OPC.

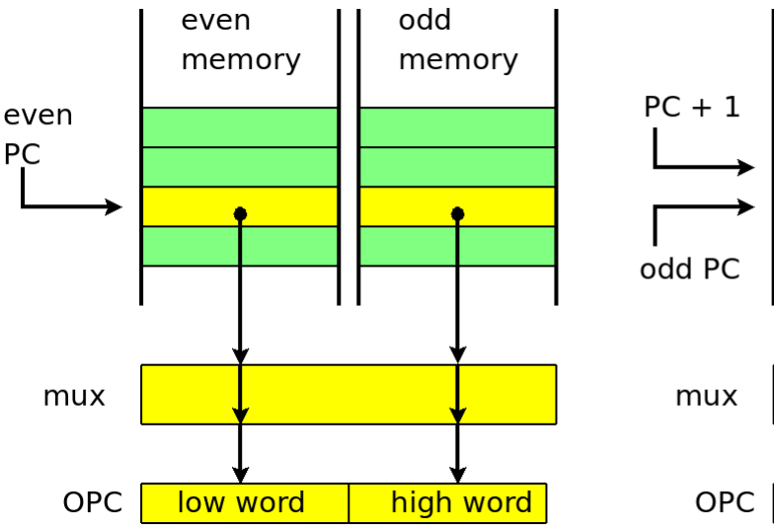
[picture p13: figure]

We observe the following:

- the odd memory address is PC[10:1] in both cases.
- the even memory address is PC[10:1] + PC[0] in both cases.
- the data outputs of the two memories are either straight or crossed, depending (only) on PC[0].

### 5 OPCODE FETCH

30

In VHDL, we express this like:

252 | L_PC_O | <= I_PC(10 downto 1);
253 | L_PC_E | <= I_PC(10 downto 1) + ("000000000" & I_PC(0));
254 | Q_OPC(15 downto | 0) | <= M_OPC_E when L_PC_0 = '0' else M_OPC_O;
255 | Q_OPC(31 downto 16) | <= M_OPC_E when L_PC_0 = '1' else M_OPC_O;

src/prog_mem.vhd

The output multiplexer uses the PC and PM_ADR of the previous cycle, so we need to remember the lower bit(s) in signals PC_0 and PM_ADR_1_0:

224 pc0: process(I_CLK)
225 begin
226 if (rising_edge(I_CLK)) then
227 | Q_PC | <= I_PC;
228 | L_PM_ADR_1_0 | <= I_PM_ADR(1 downto 0);
229 if ((I_WAIT = '0')) then
230 | L_PC_0 | <= I_PC(0);
231 end if;
232 end if;
233 end process;

src/prog_mem.vhd

The split into two memories makes the entire program memory 32-bit wide. Note that the PC is a word address, while PM_ADR is a byte address.

5.2.3 Memory block instantiation and initialization.

The entire program memory consists of 8 memory modules, four for the even half (components pe_0, pe_1, pe_2, and pe_3) and four for the odd part (po_0, po_1, po_2, and po_3).

We explain the first module in detail:

102 pe_0 : RAMB4_S4_S4 ---------------------------------------------------------103 generic map(INIT_00 => pe_0_00, INIT_01 => pe_0_01, INIT_02 => pe_0_02, 104 INIT_03 => pe_0_03, INIT_04 => pe_0_04, INIT_05 => pe_0_05, 105 INIT_06 => pe_0_06, INIT_07 => pe_0_07, INIT_08 => pe_0_08, 106 INIT_09 => pe_0_09, INIT_0A => pe_0_0A, INIT_0B => pe_0_0B, 107 INIT_0C => pe_0_0C, INIT_0D => pe_0_0D, INIT_0E => pe_0_0E, 108 INIT_0F => pe_0_0F)

### 5 OPCODE FETCH

31

109 | port map(ADDRA => L_PC_E, | ADDRB => I_PM_ADR(11 downto 2),
110 | CLKA | => I_CLK, | CLKB | => I_CLK,
111 | DIA | => "0000", | DIB | => "0000",
112 | ENA | => L_WAIT_N, | ENB | => '1',
113 | RSTA | => '0', | RSTB | => '0',
114 | WEA | => '0', | WEB | => '0',
115 | DOA | => M_OPC_E(3 downto 0), | DOB | => M_PMD_E(3 downto 0));

src/prog_mem.vhd

The first line instantiates a module of type RAMB4_S4_S4, which is a dual-port memory module with two 4-bit ports. For a Xilinx FPGA you can used these modules directly by uncommenting the use of the UNISIM library. For functional simulation we have provided a RAMB4_S4_S4.vhd component in the test directory. This component emulates the real RAMB4_S4_S4 as good as needed.

The next lines define the content of each memory module by means of a generic map. The elements of the generic map (like pe_0_00, pe_0_01, and so forth) define the initial memory content of the instantiated module. pe_0_00, pe_0_01, .. are themselves defined in prog_mem_content.vhd which is included in the library section:

34 use work.prog_mem_content.all;

src/prog_mem.vhd

The process from a C (or C++) source file hello.c to the final FPGA is then:

- write, compile, and link hello.c (produces hello.hex).
generate prog_mem_content.vhd from hello.hex (by means of tool make_mem, which is provided with this lecture).

•

- simulate, synthesize and implement the design.
- create a bitmap file.
- flash the FPGA (or serial PROM).

There are other ways of initializing the memory modules, such as updating sections of the bitmap file, but we found the above sequence easier to use.

After the generic map, follows the port map of the memory module. The two addresses ADDRA and ADDRB of the two ports come from the PC and PM_ADR inputs as already described.

Both ports are clocked from CLK. Since the program memory is read-only, the DIA and DIB inputs are not used (set to 0000) and WEA and WEB are 0. RSTA and RSTB are not used either and are set to 0. ENA is used for keeping the OPC when the pipeline is stopped, while ENB is not used. The memory outputs DOA and DOB go to the output multiplexers of the two ports.

### 5 OPCODE FETCH

32

## 5.2.3 Delayed PC

Q_PC is I_PC delayed by one clock. The program memory is a synchronous memory, which has the consequence that the program memory output OPC for a given I_PC is always one clock cycle behind as shown in the figure below on the left.

By clocking I_PC once, we re-align Q_PC and OPC as shown on the right:

227 | Q_PC | <= I_PC;

src/prog_mem.vhd

## 5.3 Two Cycle Opcodes

The vast majority of instructions executes in one cycle. Some need two cycles because they involve reading of a synchronous memory. For these signals WAIT signal is generated on the first cycle:

114 -- Two cycle opcodes:
115 --
116 -- 1001 000d dddd .... - LDS etc. 117 -- 1001 0101 0000 1000 - RET 118 -- 1001 0101 0001 1000 - RETI 119 -- 1001 1001 AAAA Abbb - SBIC 120 -- 1001 1011 AAAA Abbb - SBIS 121 -- 1111 110r rrrr 0bbb - SBRC
122 -- 1111 111r rrrr 0bbb - SBRS
123 --
124 | L_WAIT | <= '0' | when (L_INVALIDATE = '1')
125 | else '0' | when (I_INTVEC(5) | = '1')
126 | else L_T0 when ((P_OPC(15 downto | 9) = "1001000" ) | -- LDS etc.
127 | or | (P_OPC(15 downto | 8) = "10010101") | -- RET etc.
128 | or | ((P_OPC(15 downto 10) = "100110") | -- SBIC, SBIS
129 and P_OPC(8) = '1')

### 5 OPCODE FETCH

33

130 | or | (P_OPC(15 downto | 10) = "111111")) | -- SBRC, SBRS
131 | else | '0';

src/opc_fetch.vhd

## 5.4 Interrupts

The opcode fetch stage is also responsible for part of the interrupt handling. Interrupts are generated in the I/O block by setting INTVEC to a value with the highest bit set:

169 | L_INTVEC | <= "101011"; | -- _VECTOR(11)
170 end if;
171 elsif (L_TX_INT_ENABLED and not U_TX_BUSY) = '1' then
172 | if (L_INTVEC(5) = '0') then | -- no interrupt pending
173 | L_INTVEC | <= "101100"; | -- _VECTOR(12)
174 end if;
175 | else | -- no interrupt
176 | L_INTVEC | <= "000000";

src/io.vhd

The highest bit of INTVEC indicates that the lower bits contain a valid interrupt number. INTVEC proceeds to the cpu core where the upper bit is and'ed with the global interrupt enable bit (in the status register):

241 | L_INTVEC_5 | <= I_INTVEC(5) and R_INT_ENA;

src/cpu_core.vhd

The (possibly modified) INTVEC then proceeds to the opcode fetch stage. If the the global interrupt enable bit was set, then the next valid opcode is replaced by an "interrupt opcode":

135 | Q_OPC | <= X"00000000" when (L_INVALIDATE = '1')
136 | else P_OPC | when (I_INTVEC(5) = '0')
137 | else (X"000000" & "00" & I_INTVEC); | -- "interrupt opcode"

src/opc_fetch.vhd

### 5 OPCODE FETCH

34

The interrupt opcode uses a gap after the NOP instruction in the opcode set of the AVR CPU. When the interrupt opcode reaches the execution stage then is causes a branch to the location determined by the lower bits of INTVEC, pushes the program counter, and clears the interrupt enable bit. This happens a few clock cycles later. In the meantime the opcode fetch stage keeps inserting interrupt instructions into the pipeline. These additional interrupt instructions are being invalidated by the execution stage when the first interrupt instruction reaches the execution stage.

### 5 OPCODE FETCH

35

### 5 OPCODE FETCH

36

# 6 DATA PATH

In this lesson we will describe the data path of the CPU. We discuss the basic elements of the data path, but without reference to particular instructions. The implementation of instructions will be discussed in the next lesson. In this lesson we are more interested in the capabilities of the data path.

The data path consists of 3 major components: a register file, an ALU (arithmetic/logic unit), and the data memory:

37

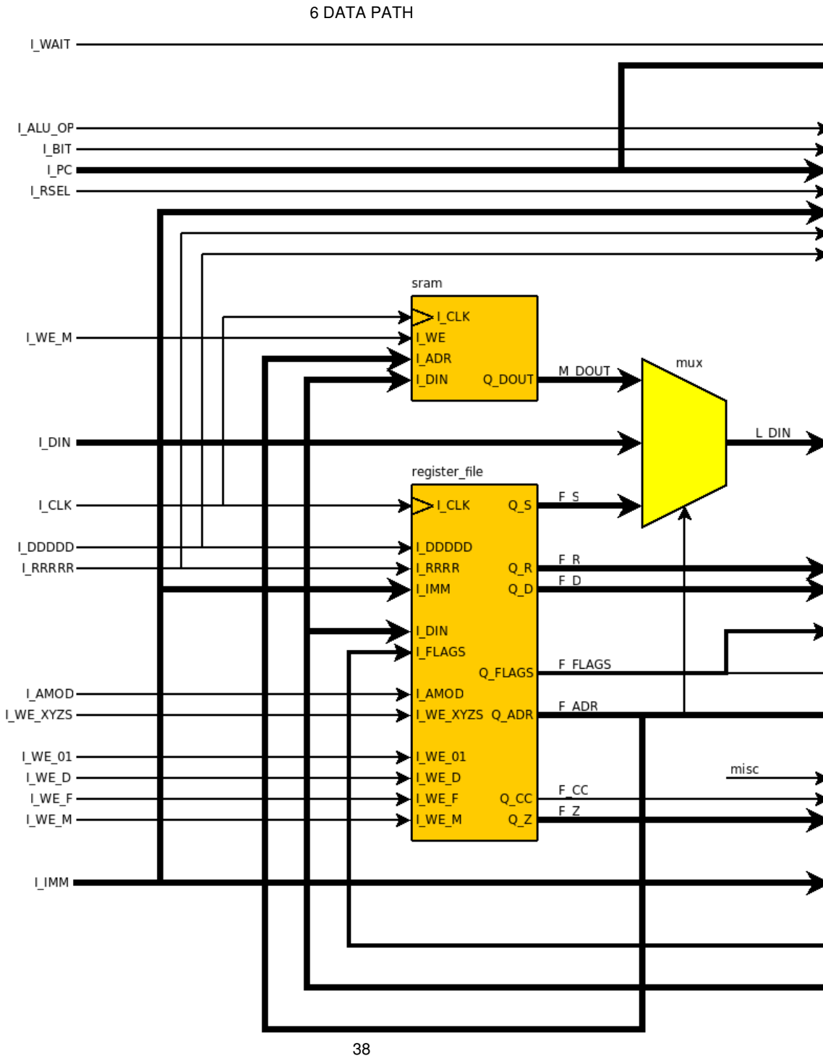
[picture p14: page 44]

### 6 DATA PATH

38

## 6.1 Register File

The AVR CPU has 32 general purpose 8-bit registers. Most opcodes use individual 8-bit registers, but some that use a pair of registers. The first register of a register pair is always an even register, while the other register of a pair is the next higher odd register. Instead of using 32 8-bit registers, we use 16 16-bit register pairs. Each register pair consists of two 8-bit registers.

## 6.1.1 Register Pair

A single register pair is defined as:

### 32 entity reg_16 is

33 | port ( | I_CLK | : in | std_logic;
34
35 | | I_D | : in | std_logic_vector (15 downto 0);
36 | | I_WE | : in | std_logic_vector ( 1 downto 0);
37
38 | Q | : out std_logic_vector (15 downto 0));
39 end reg_16;

reg_16.vhd

The Q output provides the current value of the register pair. There is no need for a read strobe, because (unlike I/O devices) reading the current value of a register pair has no side effects.

The register pair can be written by setting one or both bits of the WE input. If both bits are set then the all 16 bits of D are written; the low byte to the even register and the higher byte to the odd register of the pair. If only one bit is set then the register corresponding then the bit set in WE defines the register to be written (even bit = even register, odd bit = odd register) and the value to be written is in the lower byte of DIN:

### 46 process(I_CLK) 47 begin 48 if (rising_edge(I_CLK)) then 49 if (I_WE(1) = '1') then

50 | L(15 downto 8) | <= I_D(15 downto 8);
51 end if;

### 52 if (I_WE(0) = '1') then

53 | L( 7 downto 0) | <= I_D( 7 downto 0);
54 end if;
55 end if;
56 end process;

src/reg_16.vhd

### 6 DATA PATH

39

## 6.1.2 The Status Register

The status register is an 8-bit register. This register can be updated by writing to address 0x5F. Primarily it is updated, however, as a side effect of the execution of ALU operations. If, for example, an arithmetic/logic instruction produces a result of 0, then the zero flag (the second bit in the status register) is set. An arithmetic overflow in an ADD instruction causes the carry bit to be set, and so on. The status register is declared as:

### 32 entity status_reg is

33 | port ( | I_CLK | : in | std_logic;
34
35 | | I_COND | : in | std_logic_vector ( 3 downto 0);
36 | | I_DIN | : in | std_logic_vector ( 7 downto 0);
37 | | I_FLAGS | : in | std_logic_vector ( 7 downto 0);
38 | | I_WE_F | : in | std_logic;
39 | | I_WE_SR | : in | std_logic;
40
41 | Q | : out std_logic_vector ( 7 downto 0);
42 | Q_CC | : out std_logic);
43 end status_reg;

src/status_reg.vhd

If WE_FLAGS is '1' then the status register is updated as a result of an ALU operation; the new value of the status register is provided on the FLAGS input which comes from the ALU.

If WE_SR is '1' then the status register is updated as a result of an I/O write operation (like OUT or STS); the new value of the status register is provided on the DIN input.

The output Q of the status register holds the current value of the register. In addition there is a CC output that is '1' when the condition indicated by the COND input is fulfilled. This is used for conditional branch instructions. COND comes directly from the opcode for a branch instruction (bit 10 of the opcode for the "polarity" and bits 2-0 of the opcode for the bit of the status register that is being tested).

## 6.1.3 Register File Components

The register file consists of 16 general purpose register pairs r00 to r30, a stack pointer sp, and an 8-bit status register sr:

131 | r00: reg_16 port map(I_CLK => I_CLK, I_WE => L_WE( 1 downto | 0), I_D => I_DIN, Q => R_R00);
132 | r02: reg_16 port map(I_CLK => I_CLK, I_WE => L_WE( 3 downto | 2), I_D => I_DIN, Q => R_R02);
133 | r04: reg_16 port map(I_CLK => I_CLK, I_WE => L_WE( 5 downto | 4), I_D => I_DIN, Q => R_R04);
134 | r06: reg_16 port map(I_CLK => I_CLK, I_WE => L_WE( 7 downto | 6), I_D => I_DIN, Q => R_R06);
135 | r08: reg_16 port map(I_CLK => I_CLK, I_WE => L_WE( 9 downto | 8), I_D => I_DIN, Q => R_R08);
136 r10: reg_16 port map(I_CLK => I_CLK, I_WE => L_WE(11 downto 10), I_D => I_DIN, Q => R_R10);

### 6 DATA PATH

40

137 r12: reg_16 port map(I_CLK => I_CLK, I_WE => L_WE(13 downto 12), I_D => I_DIN, Q => R_R12); 138 r14: reg_16 port map(I_CLK => I_CLK, I_WE => L_WE(15 downto 14), I_D => I_DIN, Q => R_R14); 139 r16: reg_16 port map(I_CLK => I_CLK, I_WE => L_WE(17 downto 16), I_D => I_DIN, Q => R_R16); 140 r18: reg_16 port map(I_CLK => I_CLK, I_WE => L_WE(19 downto 18), I_D => I_DIN, Q => R_R18); 141 r20: reg_16 port map(I_CLK => I_CLK, I_WE => L_WE(21 downto 20), I_D => I_DIN, Q => R_R20); 142 r22: reg_16 port map(I_CLK => I_CLK, I_WE => L_WE(23 downto 22), I_D => I_DIN, Q => R_R22); 143 r24: reg_16 port map(I_CLK => I_CLK, I_WE => L_WE(25 downto 24), I_D => I_DIN, Q => R_R24);
144 | r26: reg_16 port map(I_CLK => I_CLK, I_WE => L_WE(27 downto 26), I_D => L_DX, | Q => R_R26);
145 | r28: reg_16 port map(I_CLK => I_CLK, I_WE => L_WE(29 downto 28), I_D => L_DY, | Q => R_R28);
146 | r30: reg_16 port map(I_CLK => I_CLK, I_WE => L_WE(31 downto 30), I_D => L_DZ, | Q => R_R30);

src/register_file.vhd

147 | sp: | reg_16 port map(I_CLK => I_CLK, I_WE => L_WE_SP, | I_D => L_DSP, Q => R_SP);

src/register_file.vhd

149 sr: status_reg
150 | port map( | I_CLK | => I_CLK,
151 | | I_COND | => I_COND,
152 | | I_DIN | => I_DIN(7 downto 0),
153 | | I_FLAGS | => I_FLAGS,
154 | | I_WE_F | => I_WE_F,
155 | | I_WE_SR | => L_WE_SR,
156 | | Q | => S_FLAGS,
157 | | Q_CC | => Q_CC);

src/register_file.vhd

Each register pair drives a 16-bit signal according to the (even) number of the register pair in the register file:

71 | signal R_R00 | : std_logic_vector(15 downto 0);
72 | signal R_R02 | : std_logic_vector(15 downto 0);
73 | signal R_R04 | : std_logic_vector(15 downto 0);
74 | signal R_R06 | : std_logic_vector(15 downto 0);
75 | signal R_R08 | : std_logic_vector(15 downto 0);
76 | signal R_R10 | : std_logic_vector(15 downto 0);
77 | signal R_R12 | : std_logic_vector(15 downto 0);
78 | signal R_R14 | : std_logic_vector(15 downto 0);
79 | signal R_R16 | : std_logic_vector(15 downto 0);
80 | signal R_R18 | : std_logic_vector(15 downto 0);
81 | signal R_R20 | : std_logic_vector(15 downto 0);
82 | signal R_R22 | : std_logic_vector(15 downto 0);
83 | signal R_R24 | : std_logic_vector(15 downto 0);
84 | signal R_R26 | : std_logic_vector(15 downto 0);
85 | signal R_R28 | : std_logic_vector(15 downto 0);
86 | signal R_R30 | : std_logic_vector(15 downto 0);
87 | signal R_SP | : std_logic_vector(15 downto 0); | -- stack pointer

src/register_file.vhd

### 6 DATA PATH

41

## 6.1.4 Addressing of General Purpose Registers

We address individual general purpose registers by a 5-bit value. Normally an opcode using an individual general purpose 8-bit register has a 5 bit field which is the address of the register. The opcode decoder transfers this field to its DDDDD or RRRRR output. For some opcodes not all 32 registers can be used, but only 16 (e.g. ANDI) or 8 (e.g. MUL). In these cases the register field in the opcode is smaller and the opcode decoder fills in the missing bits. Some opcodes imply particular registers (e.g. some LPM variant), and again the opcode decoder fills in the implied register number.

An opcode may address no, one, two, or three registers or pairs. If one register is addressed, then the number of that register is encoded in the DDDDD signal.
If two (or more) registers are used, then one (normally the destination register) is encoded in the DDDDD signal and the other (source) is encoded in the RRRRR signal. Opcodes with 3 registers (e.g. MUL) use an implied destination register pair (register pair 0) and two source registers encoded in the DDDDD and RRRRR signals.

## 6.1.5 Addressing of General Purpose Register Pairs

We address register pairs by addressing the even register of the pair. The address of a register pair is therefore a 5-bit value with the lowest bit cleared. The opcode normally only has a 4-bit field for a register pair and the lowest (cleared) bit is filled in by the opcode decoder. Like for individual registers it can happen that not all 16 register pairs can be addresses (e.g. ADIW). This is handles in the same way as for individual registers.

In the AVR context, the register pairs R26, R28, and R30 are also called (pointer registers) X, Y, and Z respectively.

## 6.1.6 Requirements on the Register File

If we go through the opcodes of the AVR CPU, then we see the capabilities that the register file must provide for general purpose registers (or register pairs):

Capability | Opcode (example)
Read one register, read/write another register | ADD Rd, Rr
Write one register, read/write another register | LD Rd, (X+)
Write one register, read another register | LD Rd, (X)
Read/write one register | ASR Rd
Read one register, read another register | CMP Rd, Rr
Read one register, read another register | LD Rd, Rr
Read one register | IN Rd, A
Write one register | OUT A, Rr

## 6.1.7 Reading Registers or Register Pairs

There are 4 cases:

- Read register or register pair addresses by DDDDD.
- Read register or register pair addresses by RRRRR.
- Read register addressed by the current I/O address.
- Read X, Y, or Z pointer implied by the addressing mode AMOD.

### 6 DATA PATH

42

- Read the Z pointer implied by the instruction (IJMP or ICALL).

Some of these cases can happen simultaneously. For example the ICALL instruction reads the Z register (the target address of the call) while it pushed the current PC onto the stack. Likewise, ST may need the X, Y, or Z for address calculations and a general purpose register that is to be stored in memory. For this reason we provide 5 different outputs in the register file. These outputs are addressing the general purpose registers differently (and they can be used in parallel):

- Q_D is the content of the register addressed by DDDDD.
- Q_R is the content of the register pair addressed by RRRR.
- Q_S is the content of the register addressed by ADR.
- Q_ADR is an address defined by AMOD (and may use X, Y, or Z).
- Q_X is the content of the Z register.

Q_D is one of the register pair signals as defined by DDDDD. We read the entire pair; the selection of the even/odd register within the pair is done later in the ALU based on DDDDD(0):

189 process(R_R00, R_R02, R_R04, R_R06, R_R08, R_R10, R_R12, R_R14, 190 R_R16, R_R18, R_R20, R_R22, R_R24, R_R26, R_R28, R_R30, 191 I_DDDDD(4 downto 1))
192 begin
193 case I_DDDDD(4 downto 1) is
194 | when "0000" => Q_D | <= R_R00;
195 | when "0001" => Q_D | <= R_R02;
196 | when "0010" => Q_D | <= R_R04;
197 | when "0011" => Q_D | <= R_R06;
198 | when "0100" => Q_D | <= R_R08;
199 | when "0101" => Q_D | <= R_R10;
200 | when "0110" => Q_D | <= R_R12;
201 | when "0111" => Q_D | <= R_R14;
202 | when "1000" => Q_D | <= R_R16;
203 | when "1001" => Q_D | <= R_R18;
204 | when "1010" => Q_D | <= R_R20;
205 | when "1011" => Q_D | <= R_R22;
206 | when "1100" => Q_D | <= R_R24;
207 | when "1101" => Q_D | <= R_R26;
208 | when "1110" => Q_D | <= R_R28;
209 | when others => Q_D | <= R_R30;
210 end case;
211 end process;

src/register_file.vhd

Q_R is one of the register pair signals as defined by RRRR:

215 | process(R_R00, R_R02, R_R04, | R_R06, R_R08, R_R10, R_R12, R_R14,
216 R_R16, R_R18, R_R20, R_R22, R_R24, R_R26, R_R28, R_R30, I_RRRR) 217 begin

### 6 DATA PATH

43

218 case I_RRRR is
219 | when "0000" => Q_R | <= R_R00;
220 | when "0001" => Q_R | <= R_R02;
221 | when "0010" => Q_R | <= R_R04;
222 | when "0011" => Q_R | <= R_R06;
223 | when "0100" => Q_R | <= R_R08;
224 | when "0101" => Q_R | <= R_R10;
225 | when "0110" => Q_R | <= R_R12;
226 | when "0111" => Q_R | <= R_R14;
227 | when "1000" => Q_R | <= R_R16;
228 | when "1001" => Q_R | <= R_R18;
229 | when "1010" => Q_R | <= R_R20;
230 | when "1011" => Q_R | <= R_R22;
231 | when "1100" => Q_R | <= R_R24;
232 | when "1101" => Q_R | <= R_R26;
233 | when "1110" => Q_R | <= R_R28;
234 | when others => Q_R | <= R_R30;
235 end case;
236 end process;

src/register_file.vhd

The general purpose registers, but also the stack pointer and the status register, are mapped into the data memory space:

Address | Purpose
0x00 - 0x1F | general purpose CPU registers.
0x20 - 0x5C | miscellaneous I/O registers.
0x5D | stack pointer low
0x5E | stack pointer high
0x5F | status register
0x60 - 0xFFFF | data memory
If an address corresponding to a register in the register file (i.e. a general purpose register, the stack pointer, or the status register is read, then the register shall be returned.
For example, LD Rd, R22 shall give the same result as LDS Rd, 22.

The 8-bit Q_S output contains the register addresses by ADR:

161 process(R_R00, R_R02, R_R04, R_R06, R_R08, R_R10, R_R12, R_R14, 162 R_R16, R_R18, R_R20, R_R22, R_R24, R_R26, R_R28, R_R30, 163 R_SP, S_FLAGS, L_ADR(6 downto 1))
164 begin
165 case L_ADR(6 downto 1) is
166 | when "000000" => L_S | <= R_R00;
167 | when "000001" => L_S | <= R_R02;
168 | when "000010" => L_S | <= R_R04;
169 | when "000011" => L_S | <= R_R06;
170 | when "000100" => L_S | <= R_R08;
171 | when "000101" => L_S | <= R_R10;
172 | when "000110" => L_S | <= R_R12;
173 | when "000111" => L_S | <= R_R14;

### 6 DATA PATH

44

174 | when "001000" => L_S | <= R_R16;
175 | when "001001" => L_S | <= R_R18;
176 | when "001010" => L_S | <= R_R20;
177 | when "001011" => L_S | <= R_R22;
178 | when "001100" => L_S | <= R_R24;
179 | when "001101" => L_S | <= R_R26;
180 | when "001110" => L_S | <= R_R28;
181 | when "001111" => L_S | <= R_R30;
182 | when "101111" => L_S | <= R_SP ( 7 downto 0) & X"00"; | -- SPL
183 | when others | => L_S | <= S_FLAGS & R_SP (15 downto 8); | -- SR/SPH
184 end case;
185 end process;
186

src/register_file.vhd

## 6.1.8 Writing Registers or Register Pairs

In order to write a register, we need to select the proper input (data source) and the proper WE signal. For most registers, the only possible data source is DIN which comes straight from the ALU. The pointer register pairs X, Y, and Z, however, can also be changed as a side effect of the post-increment (X+, Y+, Z+) and pre-decrement (-X, -Y, -Z) addressing modes of the LDS and STS instructions. The addressing modes are discussed in more detail in the next chapter; here it suffices to note that the X, Y, and #Z #registers get there data from DX, DY, and DZ, respectively rather than from DIN.

There is a total of 4 cases where general purpose registers are written. Three of these cases that are applicable to all general purpose registers and one case collects special cases for particular registers (the register numbers are then implied).

We compute a 32 bit write enable signal for each of the four cases and OR them together.

The first case is a write to an 8-bit register addressed by DDDDD. For this case we create the signal WE_D:

288 | L_WE_D( 0) | <= I_WE_D(0) when (I_DDDDD = "00000") else '0';
289 | L_WE_D( 1) | <= I_WE_D(0) when (I_DDDDD = "00001") else '0';
290 | L_WE_D( 2) | <= I_WE_D(0) when (I_DDDDD = "00010") else '0';
291 | L_WE_D( 3) | <= I_WE_D(0) when (I_DDDDD = "00011") else '0';
292 | L_WE_D( 4) | <= I_WE_D(0) when (I_DDDDD = "00100") else '0';
293 | L_WE_D( 5) | <= I_WE_D(0) when (I_DDDDD = "00101") else '0';
294 | L_WE_D( 6) | <= I_WE_D(0) when (I_DDDDD = "00110") else '0';
295 | L_WE_D( 7) | <= I_WE_D(0) when (I_DDDDD = "00111") else '0';
296 | L_WE_D( 8) | <= I_WE_D(0) when (I_DDDDD = "01000") else '0';
297 | L_WE_D( 9) | <= I_WE_D(0) when (I_DDDDD = "01001") else '0';
298 | L_WE_D(10) | <= I_WE_D(0) when (I_DDDDD = "01010") else '0';
299 | L_WE_D(11) | <= I_WE_D(0) when (I_DDDDD = "01011") else '0';
300 | L_WE_D(12) | <= I_WE_D(0) when (I_DDDDD = "01100") else '0';
301 | L_WE_D(13) | <= I_WE_D(0) when (I_DDDDD = "01101") else '0';
302 | L_WE_D(14) | <= I_WE_D(0) when (I_DDDDD = "01110") else '0';
303 | L_WE_D(15) | <= I_WE_D(0) when (I_DDDDD = "01111") else '0';
304 | L_WE_D(16) | <= I_WE_D(0) when (I_DDDDD = "10000") else '0';
305 | L_WE_D(17) | <= I_WE_D(0) when (I_DDDDD = "10001") else '0';
306 | L_WE_D(18) | <= I_WE_D(0) when (I_DDDDD = "10010") else '0';

### 6 DATA PATH

45

307 | L_WE_D(19) | <= I_WE_D(0) when (I_DDDDD = "10011") else '0';
308 | L_WE_D(20) | <= I_WE_D(0) when (I_DDDDD = "10100") else '0';
309 | L_WE_D(21) | <= I_WE_D(0) when (I_DDDDD = "10101") else '0';
310 | L_WE_D(22) | <= I_WE_D(0) when (I_DDDDD = "10110") else '0';
311 | L_WE_D(23) | <= I_WE_D(0) when (I_DDDDD = "10111") else '0';
312 | L_WE_D(24) | <= I_WE_D(0) when (I_DDDDD = "11000") else '0';
313 | L_WE_D(25) | <= I_WE_D(0) when (I_DDDDD = "11001") else '0';
314 | L_WE_D(26) | <= I_WE_D(0) when (I_DDDDD = "11010") else '0';
315 | L_WE_D(27) | <= I_WE_D(0) when (I_DDDDD = "11011") else '0';
316 | L_WE_D(28) | <= I_WE_D(0) when (I_DDDDD = "11100") else '0';
317 | L_WE_D(29) | <= I_WE_D(0) when (I_DDDDD = "11101") else '0';
318 | L_WE_D(30) | <= I_WE_D(0) when (I_DDDDD = "11110") else '0';
319 | L_WE_D(31) | <= I_WE_D(0) when (I_DDDDD = "11111") else '0';

src/register_file.vhd

The second case is a write to a 16-bit register pair addressed by DDDD (DDDD is the four upper bits of DDDDD). For this case we create signal WE_DD:

326 | L_DDDD | <= I_DDDDD(4 downto 1);
327 | L_WE_D2 | <= I_WE_D(1) & I_WE_D(1);
328 | L_WE_DD( 1 downto | 0) | <= L_WE_D2 when (L_DDDD = "0000") else "00";
329 | L_WE_DD( 3 downto | 2) | <= L_WE_D2 when (L_DDDD = "0001") else "00";
330 | L_WE_DD( 5 downto | 4) | <= L_WE_D2 when (L_DDDD = "0010") else "00";
331 | L_WE_DD( 7 downto | 6) | <= L_WE_D2 when (L_DDDD = "0011") else "00";
332 | L_WE_DD( 9 downto | 8) | <= L_WE_D2 when (L_DDDD = "0100") else "00";
333 | L_WE_DD(11 downto 10) | <= L_WE_D2 when (L_DDDD = "0101") else "00";
334 | L_WE_DD(13 downto 12) | <= L_WE_D2 when (L_DDDD = "0110") else "00";
335 | L_WE_DD(15 downto 14) | <= L_WE_D2 when (L_DDDD = "0111") else "00";
336 | L_WE_DD(17 downto 16) | <= L_WE_D2 when (L_DDDD = "1000") else "00";
337 | L_WE_DD(19 downto 18) | <= L_WE_D2 when (L_DDDD = "1001") else "00";
338 | L_WE_DD(21 downto 20) | <= L_WE_D2 when (L_DDDD = "1010") else "00";
339 | L_WE_DD(23 downto 22) | <= L_WE_D2 when (L_DDDD = "1011") else "00";
340 | L_WE_DD(25 downto 24) | <= L_WE_D2 when (L_DDDD = "1100") else "00";
341 | L_WE_DD(27 downto 26) | <= L_WE_D2 when (L_DDDD = "1101") else "00";
342 | L_WE_DD(29 downto 28) | <= L_WE_D2 when (L_DDDD = "1110") else "00";
343 | L_WE_DD(31 downto 30) | <= L_WE_D2 when (L_DDDD = "1111") else "00";

src/register_file.vhd

The third case is writing to the memory mapped I/O space of the general purpose registers. It is similar to the first case, but now we select the register by ADR instead of DDDDD. When reading from the I/O mapped register above we did not check if ADR was completely correct (and different addresses could read the same register. This was OK, since some multiplexer somewhere else would discard the value read for addresses outside the range from 0x00 to 0x1F. When writing we have to be more careful and check the range by means of WE_A. For the third case we use signal WE_IO:

### 6 DATA PATH

46

350 | L_WE_IO( 0) | <= L_WE_A when (L_ADR(4 downto 0) = "00000") else '0';
351 | L_WE_IO( 1) | <= L_WE_A when (L_ADR(4 downto 0) = "00001") else '0';
352 | L_WE_IO( 2) | <= L_WE_A when (L_ADR(4 downto 0) = "00010") else '0';
353 | L_WE_IO( 3) | <= L_WE_A when (L_ADR(4 downto 0) = "00011") else '0';
354 | L_WE_IO( 4) | <= L_WE_A when (L_ADR(4 downto 0) = "00100") else '0';
355 | L_WE_IO( 5) | <= L_WE_A when (L_ADR(4 downto 0) = "00101") else '0';
356 | L_WE_IO( 6) | <= L_WE_A when (L_ADR(4 downto 0) = "00110") else '0';
357 | L_WE_IO( 7) | <= L_WE_A when (L_ADR(4 downto 0) = "00111") else '0';
358 | L_WE_IO( 8) | <= L_WE_A when (L_ADR(4 downto 0) = "01000") else '0';
359 | L_WE_IO( 9) | <= L_WE_A when (L_ADR(4 downto 0) = "01001") else '0';
360 | L_WE_IO(10) | <= L_WE_A when (L_ADR(4 downto 0) = "01010") else '0';
361 | L_WE_IO(11) | <= L_WE_A when (L_ADR(4 downto 0) = "01011") else '0';
362 | L_WE_IO(12) | <= L_WE_A when (L_ADR(4 downto 0) = "01100") else '0';
363 | L_WE_IO(13) | <= L_WE_A when (L_ADR(4 downto 0) = "01101") else '0';
364 | L_WE_IO(14) | <= L_WE_A when (L_ADR(4 downto 0) = "01110") else '0';
365 | L_WE_IO(15) | <= L_WE_A when (L_ADR(4 downto 0) = "01111") else '0';
366 | L_WE_IO(16) | <= L_WE_A when (L_ADR(4 downto 0) = "10000") else '0';
367 | L_WE_IO(17) | <= L_WE_A when (L_ADR(4 downto 0) = "10001") else '0';
368 | L_WE_IO(18) | <= L_WE_A when (L_ADR(4 downto 0) = "10010") else '0';
369 | L_WE_IO(19) | <= L_WE_A when (L_ADR(4 downto 0) = "10011") else '0';
370 | L_WE_IO(20) | <= L_WE_A when (L_ADR(4 downto 0) = "10100") else '0';
371 | L_WE_IO(21) | <= L_WE_A when (L_ADR(4 downto 0) = "10101") else '0';
372 | L_WE_IO(22) | <= L_WE_A when (L_ADR(4 downto 0) = "10110") else '0';
373 | L_WE_IO(23) | <= L_WE_A when (L_ADR(4 downto 0) = "10111") else '0';
374 | L_WE_IO(24) | <= L_WE_A when (L_ADR(4 downto 0) = "11000") else '0';
375 | L_WE_IO(25) | <= L_WE_A when (L_ADR(4 downto 0) = "11001") else '0';
376 | L_WE_IO(26) | <= L_WE_A when (L_ADR(4 downto 0) = "11010") else '0';
377 | L_WE_IO(27) | <= L_WE_A when (L_ADR(4 downto 0) = "11011") else '0';
378 | L_WE_IO(28) | <= L_WE_A when (L_ADR(4 downto 0) = "11100") else '0';
379 | L_WE_IO(29) | <= L_WE_A when (L_ADR(4 downto 0) = "11101") else '0';
380 | L_WE_IO(30) | <= L_WE_A when (L_ADR(4 downto 0) = "11110") else '0';
381 | L_WE_IO(31) | <= L_WE_A when (L_ADR(4 downto 0) = "11111") else '0';

src/register_file.vhd

The last case for writing is handled by WE_MISC. The various multiplication opcodes write their result to register pair 0; this case is indicated the the WE_01 input. Then we have the pre-decrement and post-increment addressing modes that update the X, Y, or Z register:

389 | L_WE_X | <= I_WE_XYZS when (I_AMOD(3 downto 0) = AM_WX) else '0';
390 | L_WE_Y | <= I_WE_XYZS when (I_AMOD(3 downto 0) = AM_WY) else '0';
391 | L_WE_Z | <= I_WE_XYZS when (I_AMOD(3 downto 0) = AM_WZ) else '0';
392 | L_WE_MISC | <= L_WE_Z & L_WE_Z & | -- -Z and Z+ address modes | r30
393 | L_WE_Y & L_WE_Y & | -- -Y and Y+ address modes | r28
394 | L_WE_X & L_WE_X & | -- -X and X+ address modes | r26
395 | X"000000" & | -- never | r24 - r02
396 | I_WE_01 & I_WE_01; | -- multiplication result | r00

src/register_file.vhd

The final WE signal is then computed by or'ing the four cases above:

### 6 DATA PATH

47

398 | L_WE | <= L_WE_D or L_WE_DD or L_WE_IO or L_WE_MISC;

src/register_file.vhd

The stack pointer can be updated from two sources: from DIN as a memory mapped I/O or implicitly from XYZS by addressing modes (e.g. for CALL, RET, PUSH, and POP instructions) that write to the SP (AM_WS).

280 | L_DSP | <= L_XYZS when (I_AMOD(3 downto 0) = AM_WS) else I_DIN;

src/register_file.vhd

The status register can be written as memory mapped I/O from the DIN input or from the FLAGS input (from the ALU). The WE_SR input (for memory mapped I/O) and the WE_FLAGS input (for flags set as side effect of ALU operations) control from where the new value comes:

272 | L_WE_SR | <= I_WE_M when (L_ADR = X"005F") else '0';

src/register_file.vhd

152 | I_DIN | => I_DIN(7 downto 0),
153 | I_FLAGS | => I_FLAGS,
154 | I_WE_F | => I_WE_F,

src/register_file.vhd

## 6.1.9 Addressing Modes

The CPU provides a number of addressing modes. An addressing mode is a way to compute an address. The address specifies a location in the program memory, the data memory, the I/O memory, or some general purpose register. Computing an address can have side effects such as incrementing or decrementing a pointer register.

The addressing mode to be used (if any) is encoded in the AMOD signal. The AMOD signal consists of two sub-fields: the address source and the address offset.

### 6 DATA PATH

48

There are 5 possible address sources:

84 | constant AS_SP | : std_logic_vector(2 downto 0) := "000"; | -- SP
85 | constant AS_Z | : std_logic_vector(2 downto 0) := "001"; | -- Z
86 | constant AS_Y | : std_logic_vector(2 downto 0) := "010"; | -- Y
87 | constant AS_X | : std_logic_vector(2 downto 0) := "011"; | -- X
88 | constant AS_IMM : std_logic_vector(2 downto 0) := "100"; | -- IMM

src/common.vhd

The address sources AS_SP, AS_X, AS_Y, and AS_Z are the stack pointer, the X register pair, the Y register pair, or the Z register pair. The AS_IMM source is the IMM input (which was computed from the opcode in the opcode decoder).

There are 6 different address offsets. An address offset can imply a side effect like incrementing or decrementing the address source. The lowest bit of the address offset indicates whether a side effect is intended or not:

91 | constant AO_0 | : std_logic_vector(5 downto 3) := "000"; | -- as is
92 | constant AO_Q | : std_logic_vector(5 downto 3) := "010"; | -- +q
93 | constant AO_i | : std_logic_vector(5 downto 3) := "001"; | -- +1
94 | constant AO_ii | : std_logic_vector(5 downto 3) := "011"; | -- +2
95 | constant AO_d | : std_logic_vector(5 downto 3) := "101"; | -- -1
96 | constant AO_dd | : std_logic_vector(5 downto 3) := "111"; | -- -2

src/common.vhd

The address offset AO_0 does nothing; the address source is not modified. Address offset AO_Q adds some constant q to the address source; the constant q is provided on the IMM input (thus derived from the opcode). Address offsets AO_i resp. AO_ii increment the address source after the operation by 1 resp. 2 bytes. The address computed is the address source. Address offsets AO_d resp. AO_dd decrement the address source before the operation by 1 resp. 2 bytes. The address computed is the address source minus 1 or 2.

The constants AM_WX, AM_WY, AM_WZ, and AM_WS respectively indicate if the X, Y, Z, or SP registers will be updated and are used to decode the WE_XYZS signal to the register concerned and to select the proper inputs:

389 | L_WE_X | <= I_WE_XYZS when (I_AMOD(3 downto 0) = AM_WX) else '0';
390 | L_WE_Y | <= I_WE_XYZS when (I_AMOD(3 downto 0) = AM_WY) else '0';
391 | L_WE_Z | <= I_WE_XYZS when (I_AMOD(3 downto 0) = AM_WZ) else '0';
392 | L_WE_MISC | <= L_WE_Z & L_WE_Z & | -- -Z and Z+ address modes | r30
393 | L_WE_Y & L_WE_Y & | -- -Y and Y+ address modes | r28

### 6 DATA PATH

49

394 | L_WE_X & L_WE_X & | -- -X and X+ address modes | r26

src/register_file.vhd

277 | L_DX | <= L_XYZS when (L_WE_MISC(26) = '1') | else I_DIN;
278 | L_DY | <= L_XYZS when (L_WE_MISC(28) = '1') | else I_DIN;
279 | L_DZ | <= L_XYZS when (L_WE_MISC(30) = '1') | else I_DIN;
280 | L_DSP | <= L_XYZS when (I_AMOD(3 downto 0) = AM_WS) else I_DIN;

src/register_file.vhd

Not all combinations of address source and address offset occur; only the following combinations are needed:

108 | constant AMOD_ABS : std_logic_vector(5 downto 0) := AO_0 | & AS_IMM; -- IMM
109 | constant AMOD_X | : std_logic_vector(5 downto 0) := AO_0 | & AS_X; | -- (X)
110 | constant AMOD_Xq | : std_logic_vector(5 downto 0) := AO_Q | & AS_X; | -- (X+q)
111 | constant AMOD_Xi | : std_logic_vector(5 downto 0) := AO_i | & AS_X; | -- (X++)
112 | constant AMOD_dX | : std_logic_vector(5 downto 0) := AO_d | & AS_X; | -- (--X)
113 | constant AMOD_Y | : std_logic_vector(5 downto 0) := AO_0 | & AS_Y; | -- (Y)
114 | constant AMOD_Yq | : std_logic_vector(5 downto 0) := AO_Q | & AS_Y; | -- (Y+q)
115 | constant AMOD_Yi | : std_logic_vector(5 downto 0) := AO_i | & AS_Y; | -- (Y++)
116 | constant AMOD_dY | : std_logic_vector(5 downto 0) := AO_d | & AS_Y; | -- (--Y)
117 | constant AMOD_Z | : std_logic_vector(5 downto 0) := AO_0 | & AS_Z; | -- (Z)
118 | constant AMOD_Zq | : std_logic_vector(5 downto 0) := AO_Q | & AS_Z; | -- (Z+q)
119 | constant AMOD_Zi | : std_logic_vector(5 downto 0) := AO_i | & AS_Z; | -- (Z++)
120 | constant AMOD_dZ | : std_logic_vector(5 downto 0) := AO_d | & AS_Z; | -- (--Z)
121 | constant AMOD_SPi : std_logic_vector(5 downto 0) := AO_i | & AS_SP; | -- (SP++)
122 | constant AMOD_SPii: std_logic_vector(5 downto 0) := AO_ii & AS_SP; | -- (SP++)
123 | constant AMOD_dSP : std_logic_vector(5 downto 0) := AO_d | & AS_SP; | -- (--SP)
124 | constant AMOD_ddSP: std_logic_vector(5 downto 0) := AO_dd & AS_SP; | -- (--SP)

src/common.vhd

The following figure shows the computation of addresses:

### 6 DATA PATH

50

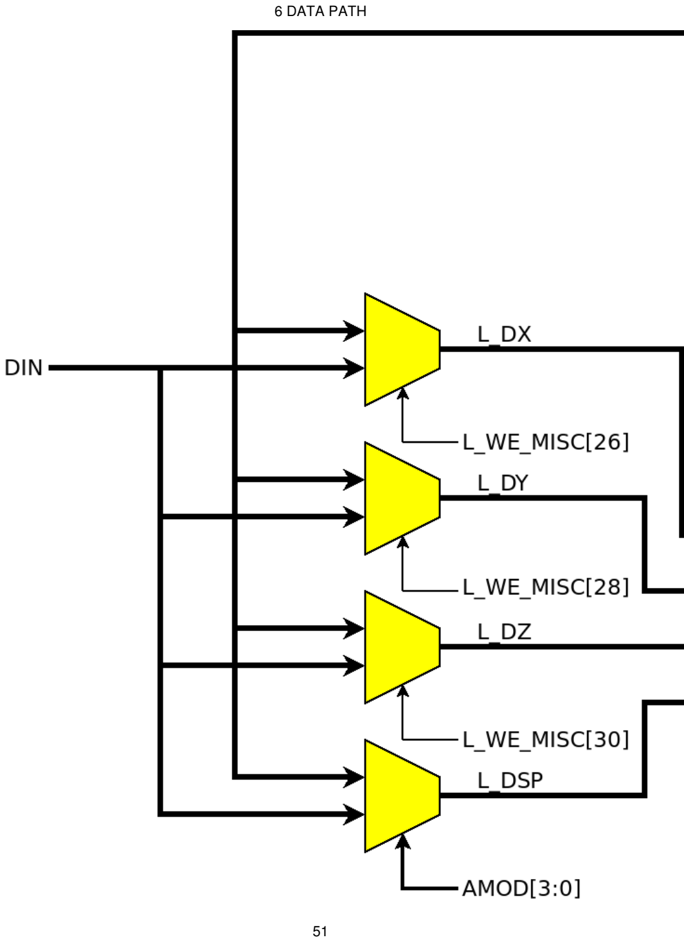
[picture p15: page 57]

### 6 DATA PATH

51

## 6.2 Data memory

The data memory is conceptually an 8-bit memory. However, some instructions (e.g. CALL, RET) write two bytes to consecutive memory locations. We do the same trick as for the program memory and divide the data memory into an even half and an odd half. The only new thing is a multiplexer at the input:

179 | L_DIN_E | <= I_DIN( 7 downto 0) when (I_ADR(0) = '0') else I_DIN(15 downto 8);
180 | L_DIN_O | <= I_DIN( 7 downto 0) when (I_ADR(0) = '1') else I_DIN(15 downto 8);

src/data_mem.vhd

The multiplexer is needed because the data memory is a read/write memory while the program memory was read-only. The multiplexer swaps the upper and lower bytes of DIN when writing to odd addresses.

## 6.3 Arithmetic/Logic Unit (ALU)

The most obvious component of a CPU is the ALU where all arithmetic and logic operations are computed. We do a little trick here and implement the data move instructions (MOV, LD, ST, etc.) as ALU operations that simply moves the data source to the output of the ALU. The data move instructions can use the same data paths as the arithmetic and logic instructions.

If we look at the instructions set of the CPU then we see that a number of instructions are quite similar. We use these similarities to reduce the number of different instructions that need to be implemented in the ALU.

- Some instructions have 8-bit and 16-bit variants (e.g. ADD and ADIW).
- Some instructions have immediate variants (e.g. CMP and CMPI).
Some instructions differ only in whether they update the destination register or not (e.g. CMP and SUB).

•

The ALU is a completely combinational circuit and therefore it has no clock input. We can divide the ALU into a number of blocks that are explained in the following.

6.3.1 D Input Multiplexing.

We have seen earlier that the D input of the ALU is the output of the register pair addressed by DDDDD[4:1] and that the D0 input of the ALU is DDDDD[0]:

178 | Q_D | => F_D,

src/data_path.vhd

### 6 DATA PATH

52

146 | I_D | => F_D,
147 | I_D0 | => I_DDDDD(0),

src/data_path.vhd

If D0 is zero, then the lower byte of the ALU operation comes from the even register regardless of the size (8-bit or 16-bit) of the operation. If D0 is odd, then the lower byte of the ALU operation comes from the odd register of the pair (and must be an 8-bit operation since register pairs always have the lowest bit of DDDDD cleared.

The upper byte of the operation (if any) is always the odd register of the pair.

We can therefore compute the lower byte, called D8, from D and D0:

356 | L_D8 | <= I_D(15 downto 8) when (I_D0 = '1') else I_D(7 downto 0);

src/alu.vhd

6.3.2 R and IMM Input Multiplexing.

Multiplexing of the R input works like multiplexing of the D input. Some opcodes can have immediate operand instead of a register addressed by RRRRR. We compute the signal R8 for opcodes that cannot have an immediate operand, and RI8 for opcodes that can have an immediate operand.

This is some fine tuning of the design: the MULT opcodes can take a while to compute but cannot have an immediate operand. It makes therefore sense to have a path from the register addressed by RRRRR to the multiplier and to put the register/immediate multiplexer outside that critical path through the ALU.

357 | L_R8 | <= I_R(15 downto 8) when (I_R0 = '1') else I_R(7 downto 0);
358 | L_RI8 | <= I_IMM | when (I_RSEL = RS_IMM) else L_R8;

src/alu.vhd

## 6.3.3 Arithmetic and Logic Functions

The first step in the computation of the arithmetic and logic functions is to compute a number of helper values. The reason for computing them beforehand is that we need these values several times, either for

### 6 DATA PATH

53 different but similar opcodes (e.g. CMP and SUB) but also for the result and for the flags of the same opcode.

360 | L_ADIW_D | <= I_D + ("0000000000" & I_IMM(5 downto 0));
361 | L_SBIW_D | <= I_D - ("0000000000" & I_IMM(5 downto 0));
362 | L_ADD_DR | <= L_D8 + L_RI8;
363 | L_ADC_DR | <= L_ADD_DR + ("0000000" & I_FLAGS(0));
364 | L_ASR_D | <= L_D8(7) & L_D8(7 downto 1);
365 | L_AND_DR | <= L_D8 and L_RI8;
366 | L_DEC_D | <= L_D8 - X"01";
367 | L_INC_D | <= L_D8 + X"01";
368 | L_LSR_D | <= '0' & L_D8(7 downto 1);
369 | L_NEG_D | <= X"00" - L_D8;
370 | L_NOT_D | <= not L_D8;
371 | L_OR_DR | <= L_D8 or L_RI8;
372 | L_PROD | <= (L_SIGN_D & L_D8) * (L_SIGN_R & L_R8);
373 | L_ROR_D | <= I_FLAGS(0) & | L_D8(7 downto 1);
374 | L_SUB_DR | <= L_D8 - L_RI8;
375 | L_SBC_DR | <= L_SUB_DR - ("0000000" & I_FLAGS(0));
376 | L_SIGN_D | <= L_D8(7) and I_IMM(6);
377 | L_SIGN_R | <= L_R8(7) and I_IMM(5);
378 | L_SWAP_D | <= L_D8(3 downto 0) & L_D8(7 downto 4);
379 | L_XOR_DR | <= L_D8 xor L_R8;

src/alu.vhd

Most values should be obvious, but a few deserve an explanation: There is a considerable number of multiplication functions that only differ in the signedness of their operands. Instead of implementing a different 8-bit multiplier for each opcode, we use a common signed 9-bit multiplier for all opcodes. The opcode decoder sets bits 6 and/or 5 of the IMM input if the D operand and/or the R operand is signed. The signs of the operands are then SIGN_D and SIGN_R; they are 0 for unsigned operations. Next the signs are prepended to the operands so that each operand is 9-bit signed. If the operand was unsigned (and the sign was
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

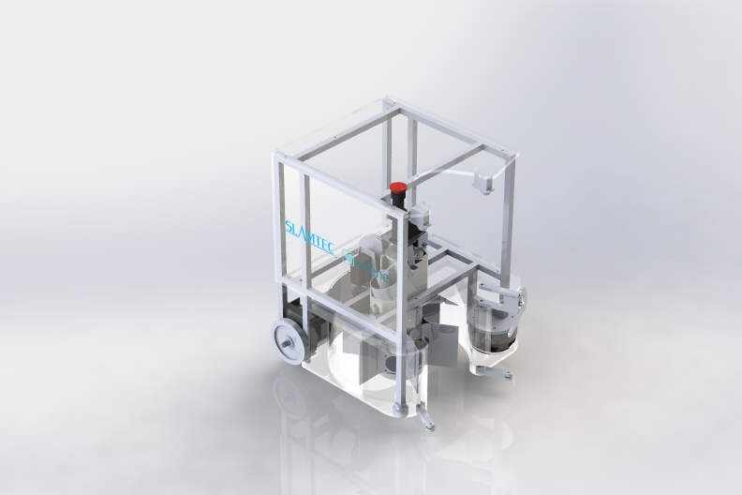
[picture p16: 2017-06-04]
meca/Images/Robot 2.JPG

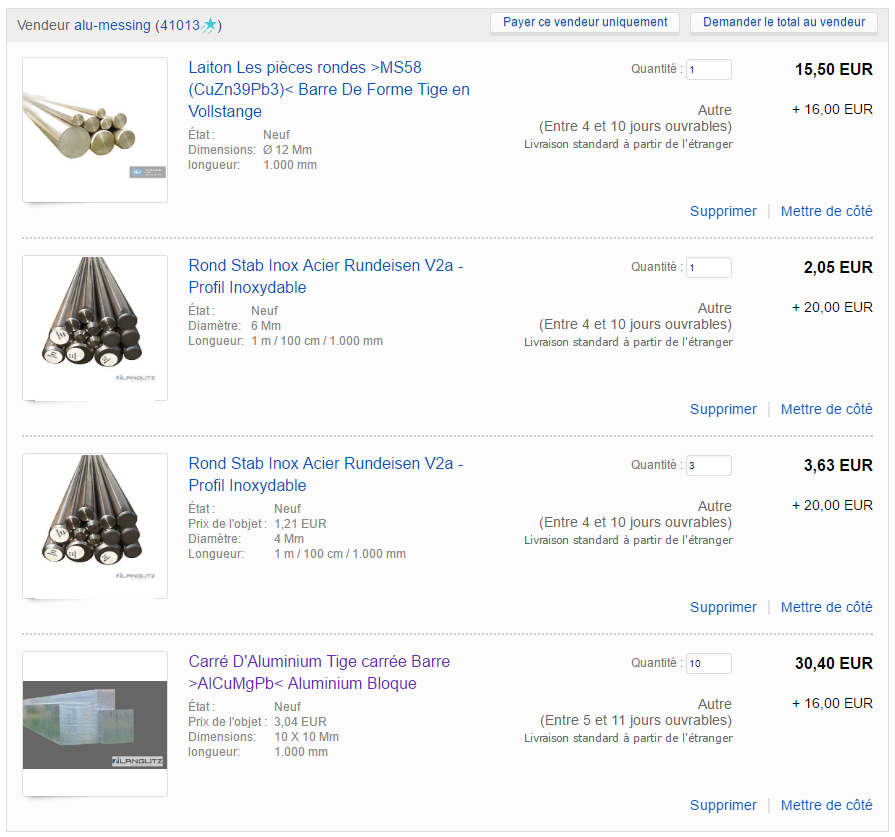
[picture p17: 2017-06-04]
admin/ebay.png

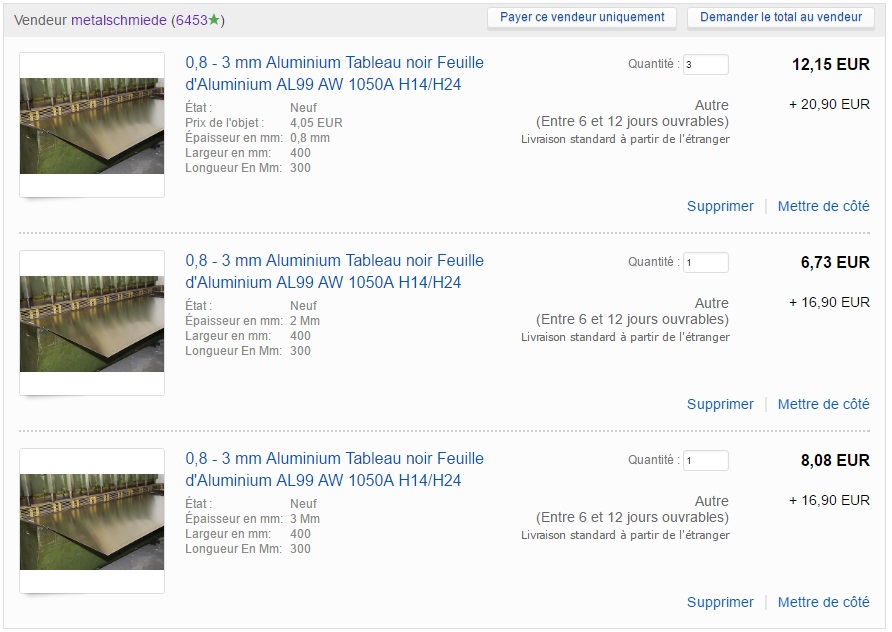
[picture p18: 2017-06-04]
admin/ebay2.jpg

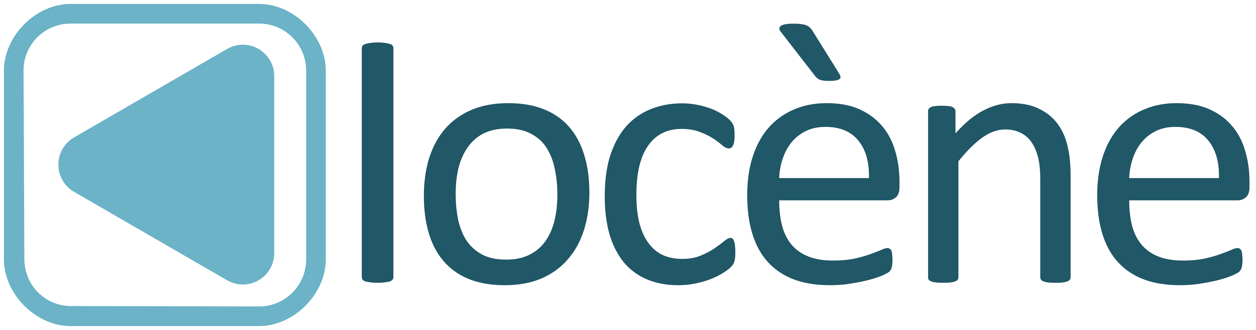
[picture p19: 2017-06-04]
meca/Iocène.png

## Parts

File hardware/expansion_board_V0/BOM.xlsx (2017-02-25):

ok | Qty | Value |  | Package | Device | Parts | Description | PROD_ID
x | 1 | FPGA_ARDUINO |  | ARDUINOR3 | ARDUINOR3-DIMENSION | U29 | This is a new object for the new Arduino R3 - with extra pins that you may want to use (such as IOref, and duplicated A4/A5
x | 1 | BUZZER |  | BUZZER_CIRCLE | BUZZER | U2
x | 92 | 100n |  | CAPC1005X55N | C_402 | C1, C3, C5, C7, C8, C9, C10, C28, C37, C46, C67, C73, C75, C89, C93, C94, C98, C99, C100, C101, C102, C103, C106, C107, C108, C109, C112, C113, C114, C115, C116, C117, C118, C122, C123, C124, C125, C129, C130, C131, C132, C133, C134, C135, C136, C137, C138, C139, C140, C141, C142, C143, C144, C145, C146, C147, C149, C152, C154, C155, C156, C157, C159, C160, C161, C162, C163, C164, C165, C167, C171, C172, C173, C174, C181, C182, C183, C184, C185, C186, C187, C188, C189, C190, C191, C192, C193, C194, C195, C216, C217, C219
x | 2 | 18p |  | CAPC1005X55N | C_402 | C150, C151
x | 3 | nc |  | CAPC1005X55N | C_402 | C19, C23, C27
x | 1 | ESC_CHINOI15A |  | ESC_CHINOI15A | ESC_CHINOI15A | U19
x | 1 | ESC_TURNIGY40A |  | ESC_TURNIGY40A | ESC_TURNIGY40A | U17
x | 7 | LED_603 |  | LEDC1608X60N | LED_603 | D4, D5, D6, D7, D8, D9, D10
x | 2 | LGA22U |  | LGA22U | LGA22U | U21, U22
x | 3 | MOSFET_NTR5198NL |  | SOT95P290X130-3N | MOSFET_NTR5198NL | T1, T2, T3
x | 4 | RELAY_V23101-SMT |  | V23101-D0103-A201-SMT | RELAY_V23101-SMT | K1, K2, K3, K4
+ | 1 | ADS1258 |  | QFN48 | ADS1258 | IC1 | edit this description
+ | 1 | ADS1278 |  | IC2 | ADS1278";TQFP64_POWERPAD" | edit this description
x | 2 | 100p |  | CAPC1005X55N | C_402 | C4, C178
x | 6 | 10n |  | CAPC1005X55N | C_402 | C57, C59, C72, C92, C97, C177
x | 17 | 1n |  | CAPC1005X55N | C_402 | C56, C58, C71, C76, C90, C95, C96, C104, C105, C110, C111, C119, C120, C121, C126, C127, C128
x | 3 | 22n |  | CAPC1005X55N | C_402 | C168, C169, C170
* | 32 | 100n | 50v | CAPC1608X95N | C_603 | C33, C34, C35, C36, C42, C43, C44, C45, C51, C52, C53, C54, C55, C60, C61, C62, C63, C64, C65, C66, C68, C69, C70, C74, C77, C78, C79, C80, C85, C86, C87, C88
x | 2 | 1u |  | CAPC1608X95N | C_603 | C175, C179
x | 16 | 1µ | 12v | CAPC1608X95N | C_603 | C29, C30, C31, C32, C38, C39, C40, C41, C47, C48, C49, C50, C81, C82, C83, C84
x | 5 | 2.2u |  | CAPC1608X95N | C_603 | C148, C153, C158, C166, C220
x | 4 | 2u |  | CAPC1608X95N | C_603 | C196, C197, C198, C199
* | 1 | 100n | 50v | CAPC2013X100N | C_805 | C11
x | 10 | 10u | 15v | CAPC2013X100N | C_805 | C13, C14, C16, C17, C20, C21, C24, C25, C176, C180
* | 1 | ELEC |  | PHOENIX381P900X920-2N | CON2_3.81 | CON1
* | 4 | LIPO_MOT |  | PHOENIX381P900X920-2N | CON2_3.81 | CON3, CON4, CON5, CON6
* | 1 | M0 |  | PHOENIX381P900X920-2N | CON2_3.81 | CON8
* | 1 | M1 |  | PHOENIX381P900X920-2N | CON2_3.81 | CON13
* | 1 | M2 |  | PHOENIX381P900X920-2N | CON2_3.81 | CON11
* | 1 | M3 |  | PHOENIX381P900X920-2N | CON2_3.81 | CON9
* | 1 | M4 |  | PHOENIX381P900X920-2N | CON2_3.81 | CON12
* | 1 | M5 |  | PHOENIX381P900X920-2N | CON2_3.81 | CON10
* | 1 | SERVO |  | PHOENIX381P900X920-2N | CON2_3.81 | CON2
x | 1 | ESC0 |  | PHOENIX381P1662X920-4N | CON4_3.81 | CON14
x | 1 | ESC1 |  | PHOENIX381P1662X920-4N | CON4_3.81 | CON17
x | 1 | 220u |  | CAPAE835X1020N | CPOL | C12
x | 7 | 470u |  | CAPAE835X1020N | CPOL | C2, C6, C15, C18, C22, C26, C91
x | 4 | DRV8432 |  | R-PDSO-G36 | DRV84X2_DRV8432 | U9, U10, U11, U14
-2 | 2 | TCA6408A |  | QFN50P300X300X80-17N | I2C_EXPTCA6408A | U34, U39
-5 | 7 | INA240-A2 |  | TSSOP | INA240-TSSOP | U7, U8, U12, U13, U15, U16, U18
* | 8 | SRN2512-R24M |  | INDC2520X120N | INDUCTANCE_2520 | L1, L2, L3, L4, L5, L6, L7, L8
x | 2 | 600 |  | INDC1608X95N | INDUCTANCE_603 | L9, L10
+ | 1 | LAN9514 |  | QFN50P900X900X100-65N | LAN9514 | U20 | edit this description
* | 1 | MPU-9250 |  | QFN24-3X3 | MPU-9250 | U37 | NC pin 19. 2-6 & 14-17 not internally connected. May be used for PCB trace routing. | IC-13192
x | 1 | OPA376 |  | SC70-5N | OPA376 | U24
x | 1 | PTR08100W |  | PTR08100W | PTR08100W | U3
* | 1 | 32.768kHz |  | 1206 | QUARTZ_1206 | Q2
* | 1 | 25MHz |  | XTAL500X320X130N | QUARTZ2 | Q1
x | 7 | 100k |  | RESC1005X40N | R_402 | R1, R2, R3, R4, R15, R17, R19
x | 55 | 10k |  | RESC1005X40N | R_402 | R21, R22, R27, R31, R34, R35, R37, R41, R42, R43, R44, R46, R47, R48, R49, R53, R54, R55, R56, R59, R60, R63, R64, R66, R67, R68, R69, R74, R75, R76, R77, R79, R80, R81, R82, R84, R85, R86, R87, R89, R91, R93, R97, R99, R100, R101, R102, R103, R104, R105, R106, R107, R108, R109, R110
x | 1 | 12.4k |  | RESC1005X40N | R_402 | R95
x | 1 | 12k |  | RESC1005X40N | R_402 | R96
x | 2 | 19k |  | RESC1005X40N | R_402 | R18, R20
x | 2 | 1M |  | RESC1005X40N | R_402 | R90, R98
x | 10 | 1k |  | RESC1005X40N | R_402 | R39, R40, R50, R51, R58, R61, R62, R71, R72, R73
* | 1 | 240 |  | RESC1005X40N | R_402 | R9
* | 4 | 30k |  | RESC1005X40N | R_402 | R26, R28, R30, R33
- | 1 | 32k |  | RESC1005X40N | R_402 | R16
x | 2 | 330 |  | RESC1005X40N | R_402 | R92, R94
x | 4 | 560 |  | RESC1005X40N | R_402 | R10, R11, R12, R13
x | 5 | 5k |  | RESC1005X40N | R_402 | R5, R6, R7, R8, R14
x | 8 | 0.01 |  | RESC1608X50AN | R_603 | R45, R52, R57, R65, R70, R78, R83, R88
x | 7 | ULR15S-R0055FT2 |  | RESC_ULR15S-R0055FT2 | R_ULR15S-R0055FT2 | R23, R24, R25, R29, R32, R36, R38
-1 | 1 | REF5025I |  | MSOP8_0.65 | REF5025I | IC4 | edit this description
x1 | 1 | REF5030I |  | MSOP8_0.65 | REF5025I | IC3 | edit this description
-4 | 2 | LP5900SD-2.8 |  | SON65P250X220X80-7N | REG_EN_LP5900 | U35, U40
-4 | 1 | LP5900_2.2 |  | SON65P250X220X80-7N | REG_EN_LP5900 | U23
-2 | 1 | LP5900_3 |  | SON65P250X220X80-7N | REG_EN_LP5900 | U38
* | 1 | SN74LV4052A_SO |  | SOIC127P780X200-16N | SN74LV4052A_SO | U1
-5 | 3 | TPS82130 |  | SON65P310X290X153-9N | TPS82130 | U4, U5, U6
-5 | 7 | TXS0108PWR |  | SOP65P640X110-20N | TX_0108_TSSOP | U25, U27, U30, U32
- | 1 | USB2 |  | USB_A | USB_A | CON54
- | 2 | USB3 |  | USB_A | USB_A | CON55, CON60
- | 1 | VL53L0X |  | VL53L0X | VL53L0X | U33
- | 1 | VL6180X |  | VL6180X | VL6180X | U36
x | 2 | SMP12A |  | DO220AA | ZENER | D1, D2
* | 1 | SMAJ51A |  | D0214AC | ZENERDO214 | D3
 | 403 | TOTAL

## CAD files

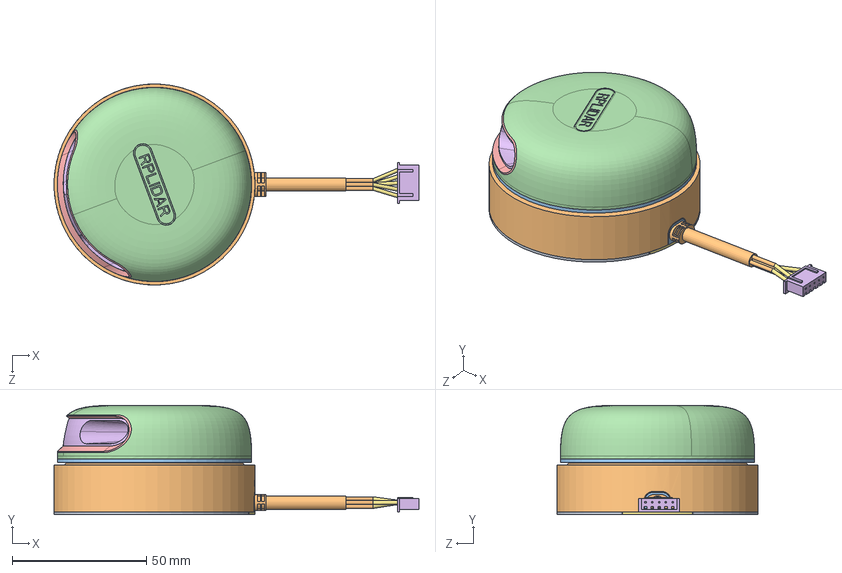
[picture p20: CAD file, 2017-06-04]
meca/Rplidar/rplidar.SLDASM
136.2 x 40.8 x 75.0 mm
µ×¸Ç
±àÂë³ÝÍâ¿Ç
Ðý×ªÆ½Ì¨
LENS_1.6
KEY_1.6
BAT_COVER_19
·â¸Ç
¼¤¹â·¢ÉäÍ·
¾µÍ·
4pinÏßÀÂ
½ÓÏß¶Ë¸Ç
6p ²åÍ·
Áã¼þ4^Íâ½ÓÏßÕûÌå
5pin 2.54²åÍ·
Áã¼þ1^Íâ½ÓÏßÕûÌå

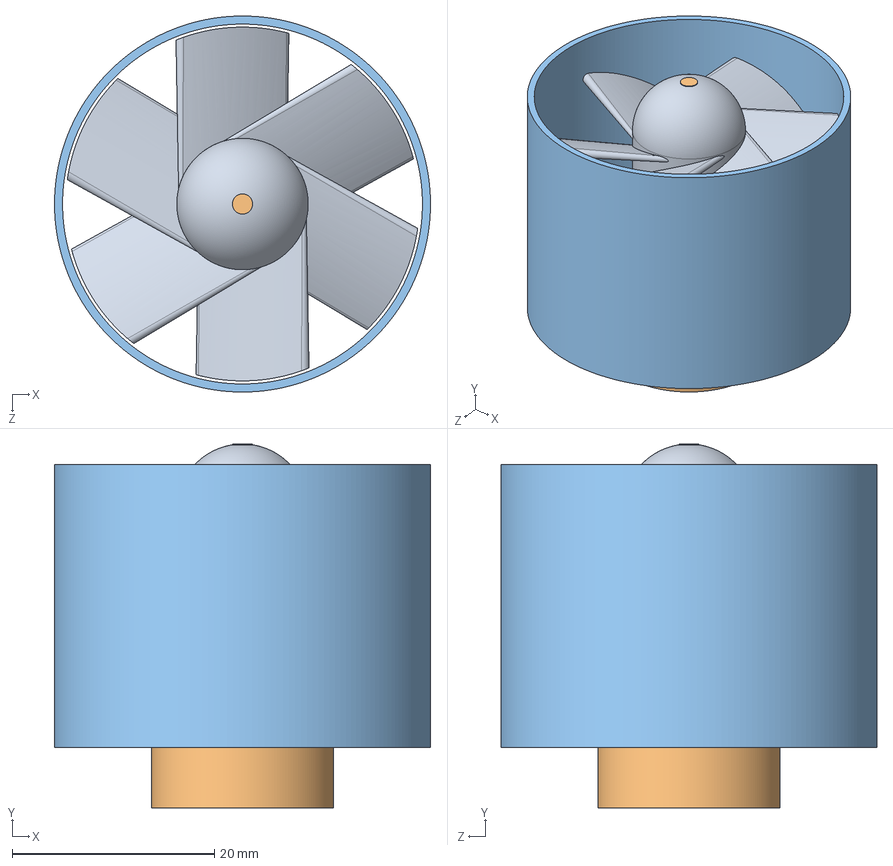
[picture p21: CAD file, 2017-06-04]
meca/Assemblage1.sldasm
37.2 x 36.0 x 37.2 mm
126 Ventillateur
125 Moteur ventillateur 2
127 Tube ventillateur

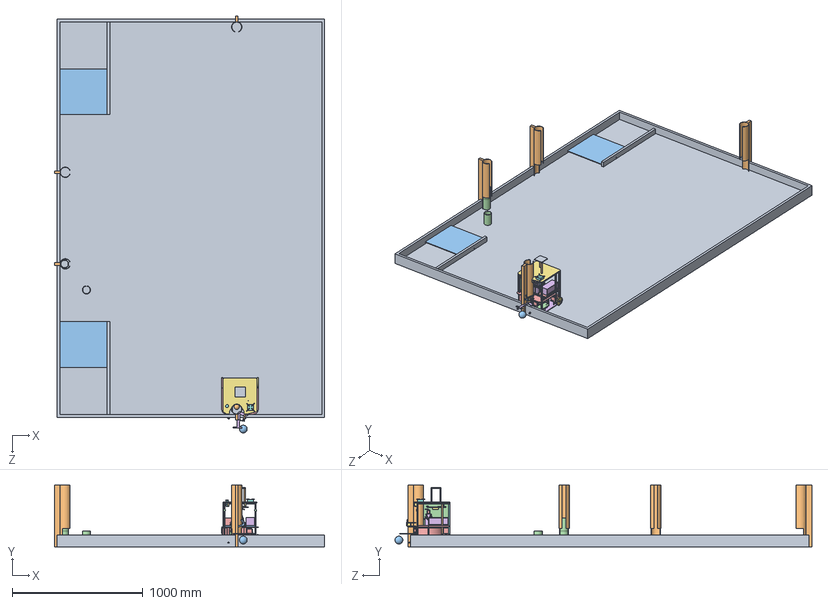
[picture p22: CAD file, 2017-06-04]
meca/00 Table.SLDASM
2066.0 x 472.0 x 3186.3 mm
01 Table
02 Fusée x 4
03 Bascule x 2
11 Module x 3
111 Moteur crouzet x 2
113 Moyeu roue x 3
112 Roue x 3
114 Roue folle
Montant codeur
Support codeur x 2
Codeur x 2
Roue codeuse x 2
µ×¸Ç
±àÂë³ÝÍâ¿Ç
Ðý×ªÆ½Ì¨
LENS_1.6
KEY_1.6
BAT_COVER_19
·â¸Ç
¼¤¹â·¢ÉäÍ·
¾µÍ·
Support télémetre
123 Extérieur carrousel
120 Support carrousel
128 Pignon caroussel
129 Pignon moteur caroussel
139 moteur carrousel
121 Centre carrousel
122 Pale carrousel x 6
124 Vis pale carrousel x 5
Servo moteur MG995 x 4
Support servo caroussel
131 Servo avant x 3
133 Barriere x 2
132 Roulement x 2
134 Support servo renverser x 2
135 Levier renverser
126 Ventillateur
125 Moteur ventillateur 2
127 Tube ventillateur
142 Verin tube 1
143 Verin tube 2
144 Verin tube 3
145 Poulie verin x 5
Roue vérin
Support servo verin
Plancher
Plancher protection balles
Plafond
Montant v1 x 2
Montant v2 x 2
Montant v3 x 2
Montant h11 x 5
Montant h12
Montant h21 x 2
Montant h22 x 2
Montant v4
21.02 AU
AS5047P
Lipo moteur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

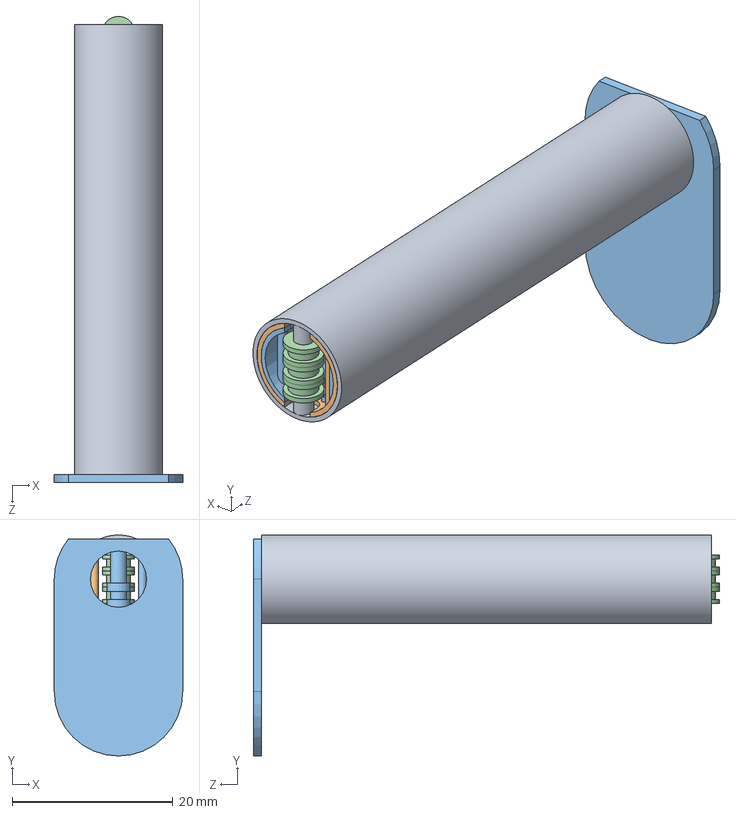
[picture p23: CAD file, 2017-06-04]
meca/141 Verin.sldasm
16.0 x 27.5 x 58.0 mm
142 Verin tube 1
143 Verin tube 2
144 Verin tube 3
145 Poulie verin x 5

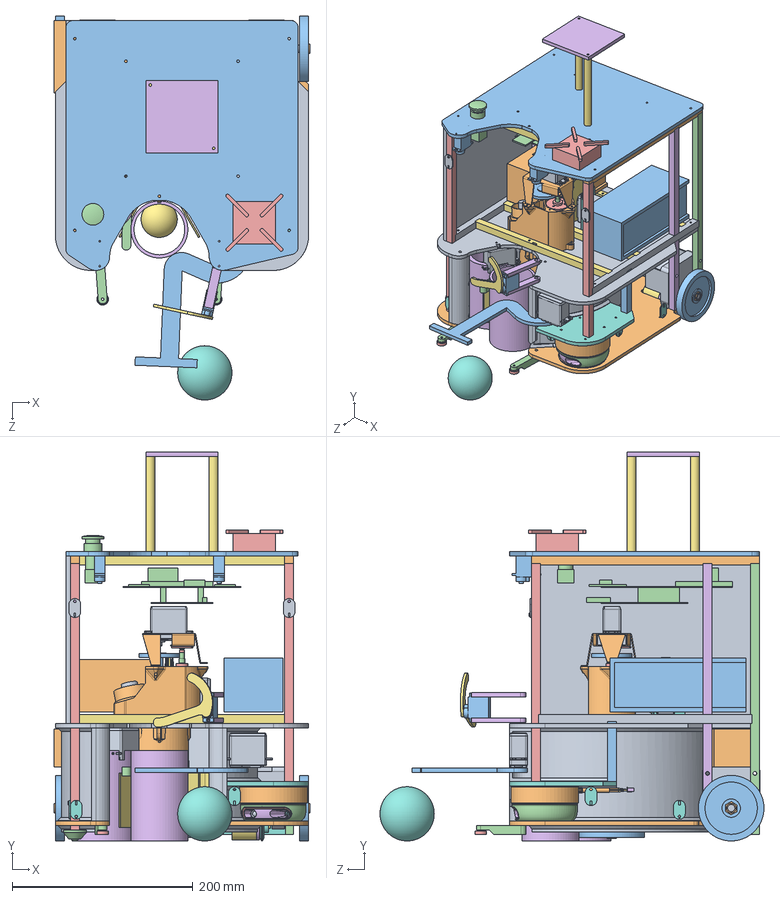
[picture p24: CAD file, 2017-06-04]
meca/100 Robot.SLDASM
282.7 x 430.0 x 424.6 mm
111 Moteur crouzet x 2
113 Moyeu roue x 3
112 Roue x 3
114 Roue folle
Montant codeur
Support codeur x 2
Codeur x 2
Roue codeuse x 2
µ×¸Ç
±àÂë³ÝÍâ¿Ç
Ðý×ªÆ½Ì¨
LENS_1.6
KEY_1.6
BAT_COVER_19
·â¸Ç
¼¤¹â·¢ÉäÍ·
¾µÍ·
Support télémetre
123 Extérieur carrousel
120 Support carrousel
128 Pignon caroussel
129 Pignon moteur caroussel
139 moteur carrousel
121 Centre carrousel
122 Pale carrousel x 6
124 Vis pale carrousel x 5
Servo moteur MG995 x 4
Support servo caroussel
131 Servo avant x 3
133 Barriere x 2
132 Roulement x 2
134 Support servo renverser x 2
135 Levier renverser
126 Ventillateur
125 Moteur ventillateur 2
127 Tube ventillateur
142 Verin tube 1
143 Verin tube 2
144 Verin tube 3
145 Poulie verin x 5
Roue vérin
Support servo verin
Plancher
Plancher protection balles
Plafond
Montant v1 x 2
Montant v2 x 2
Montant v3 x 2
Montant h11 x 5
Montant h12
Montant h21 x 2
Montant h22 x 2
Montant v4
21.02 AU
AS5047P
Lipo moteur
Lipo élec
Carte élec
Drone
Support balise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

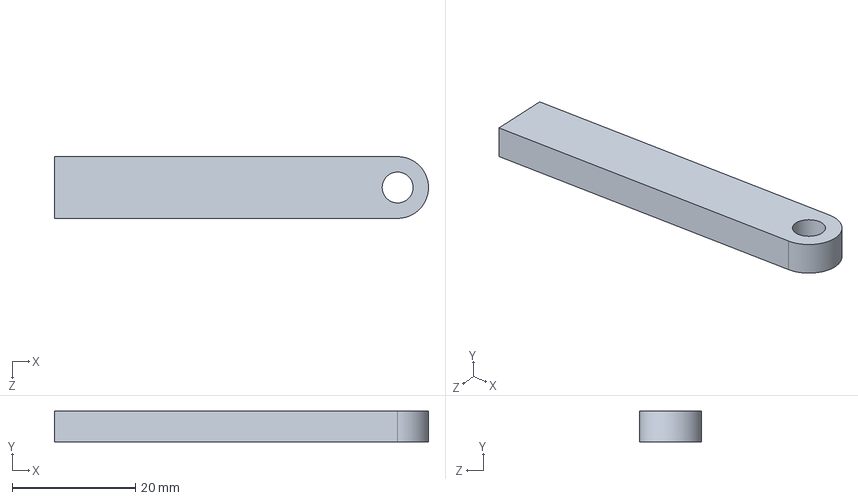
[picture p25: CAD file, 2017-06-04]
meca/134 Support servo renverser.SLDPRT
60.6 x 5.00 x 10.0 mm

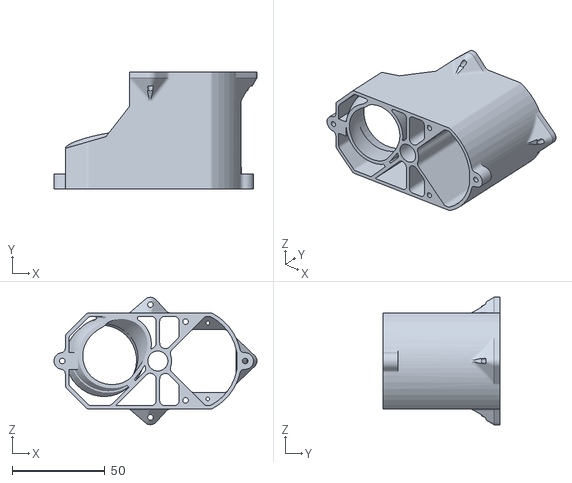
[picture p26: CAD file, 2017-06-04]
meca/stl/Support carrousel haut.STL
109.6 x 63.0 x 68.9

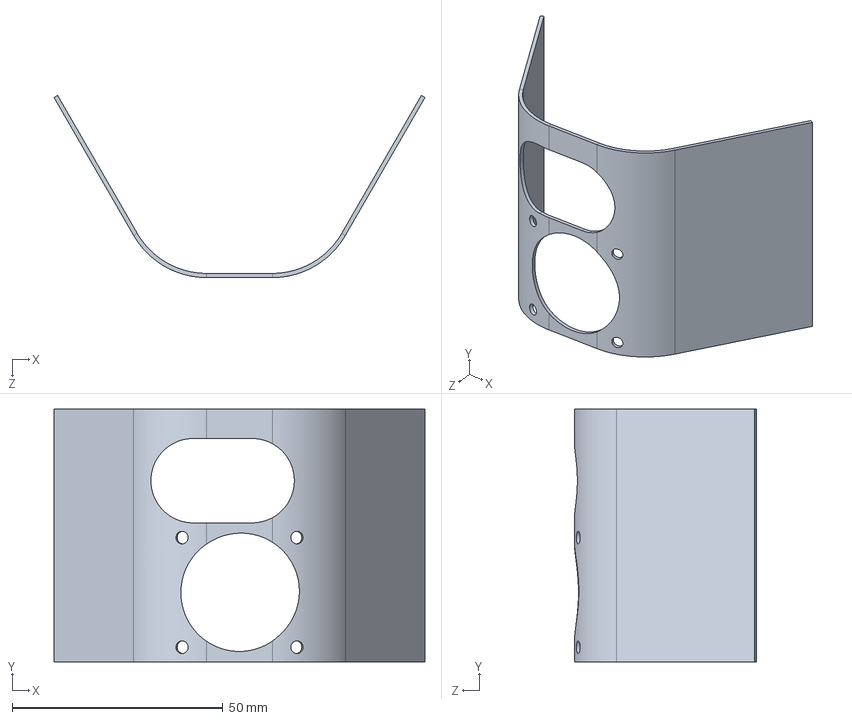
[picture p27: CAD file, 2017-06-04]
meca/122 Pale carrousel.SLDPRT
88.0 x 60.0 x 43.2 mm

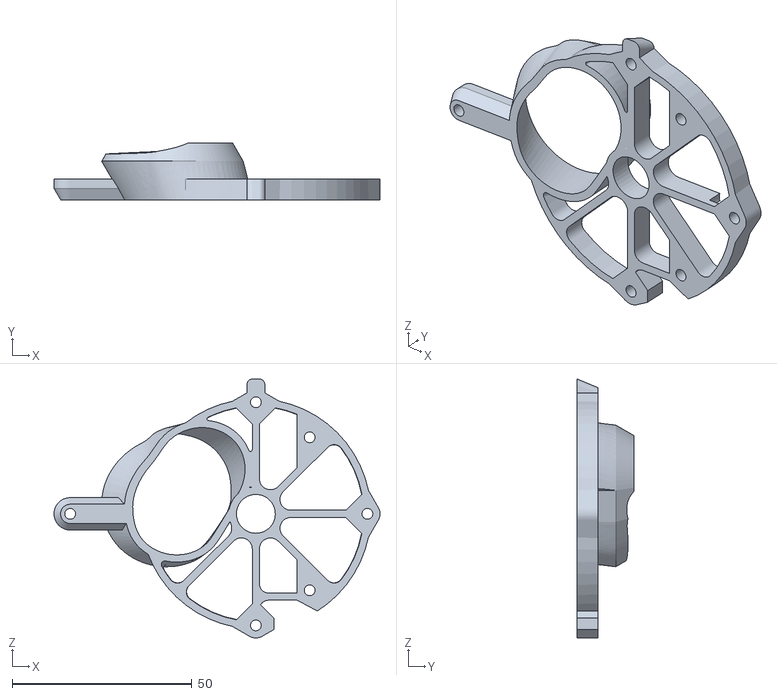
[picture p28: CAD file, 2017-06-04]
meca/stl/Support carrousel bas partie 2.STL
90.6 x 15.7 x 71.9

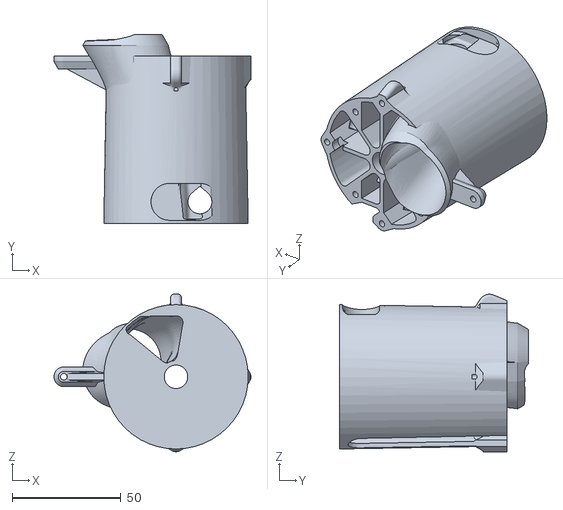
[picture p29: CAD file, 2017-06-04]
meca/stl/Support carrousel bas.STL
90.6 x 87.0 x 72.5

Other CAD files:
meca/Rplidar/Íâ½ÓÏßÕûÌå.sldasm
meca/Rplidar/RPLIDAR A2.sldasm
hardware/expansion_board_V0/FPGA board - dimensions.SLDPRT
meca/Essais/Hauteur laser.SLDPRT
meca/Rplidar/¾µÍ·.sldprt
software/HPS_FPGA_LED/fpga/stp_debug2.stp
meca/Essais/Dimensions carrousel.SLDPRT
meca/Rplidar/Áã¼þ1^Íâ½ÓÏßÕûÌå.sldprt
meca/01 Table.SLDPRT
meca/02 Fusée.SLDPRT
meca/03 Bascule.SLDPRT
meca/11 Module.SLDPRT
meca/111 Moteur crouzet.SLDPRT
meca/112 Roue.SLDPRT
meca/113 Moyeu roue.SLDPRT
meca/114 Roue folle 1.SLDPRT
meca/114 Roue folle.SLDPRT
meca/12 Roche lunaire.SLDPRT
meca/123 Extérieur carrousel.SLDPRT
meca/124 Vis pale carrousel.SLDPRT
meca/125 Moteur ventillateur 2.SLDPRT
meca/125 Moteur ventillateur.SLDPRT
meca/126 Ventillateur.SLDPRT
meca/127 Tube ventillateur.SLDPRT
meca/128 Pignon caroussel.SLDPRT
meca/129 Pignon moteur caroussel.SLDPRT
meca/13 Minerai.SLDPRT
meca/131 Servo avant.SLDPRT
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

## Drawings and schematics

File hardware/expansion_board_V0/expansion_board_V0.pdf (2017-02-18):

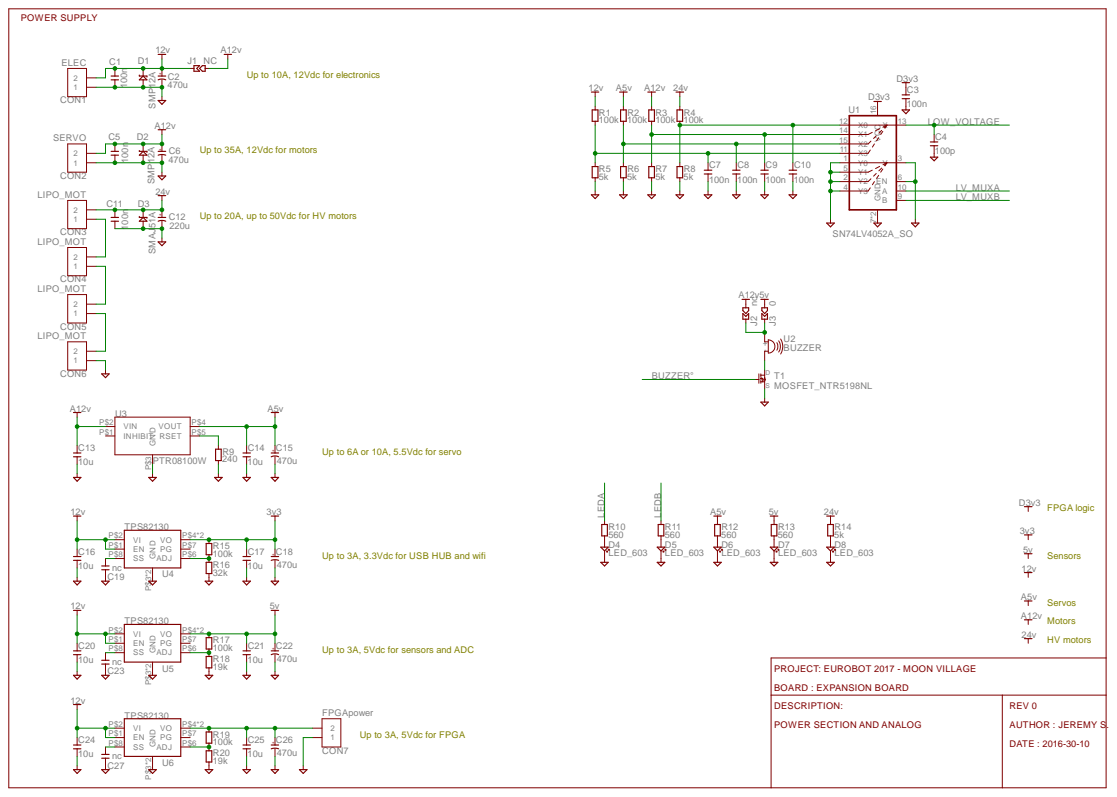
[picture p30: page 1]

Up to 10A, 12Vdc for electronics

Up to 35A, 12Vdc for motors

Up to 20A, up to 50Vdc for HV motors

Up to 6A or 10A, 5.5Vdc for servo

Up to 3A, 3.3Vdc for USB HUB and wifi

Up to 3A, 5Vdc for sensors and ADC

PROJECT: EUROBOT 2017 - MOON VILLAGE
BOARD : EXPANSION BOARD
DESCRIPTION:
POWER SECTION AND ANALOG

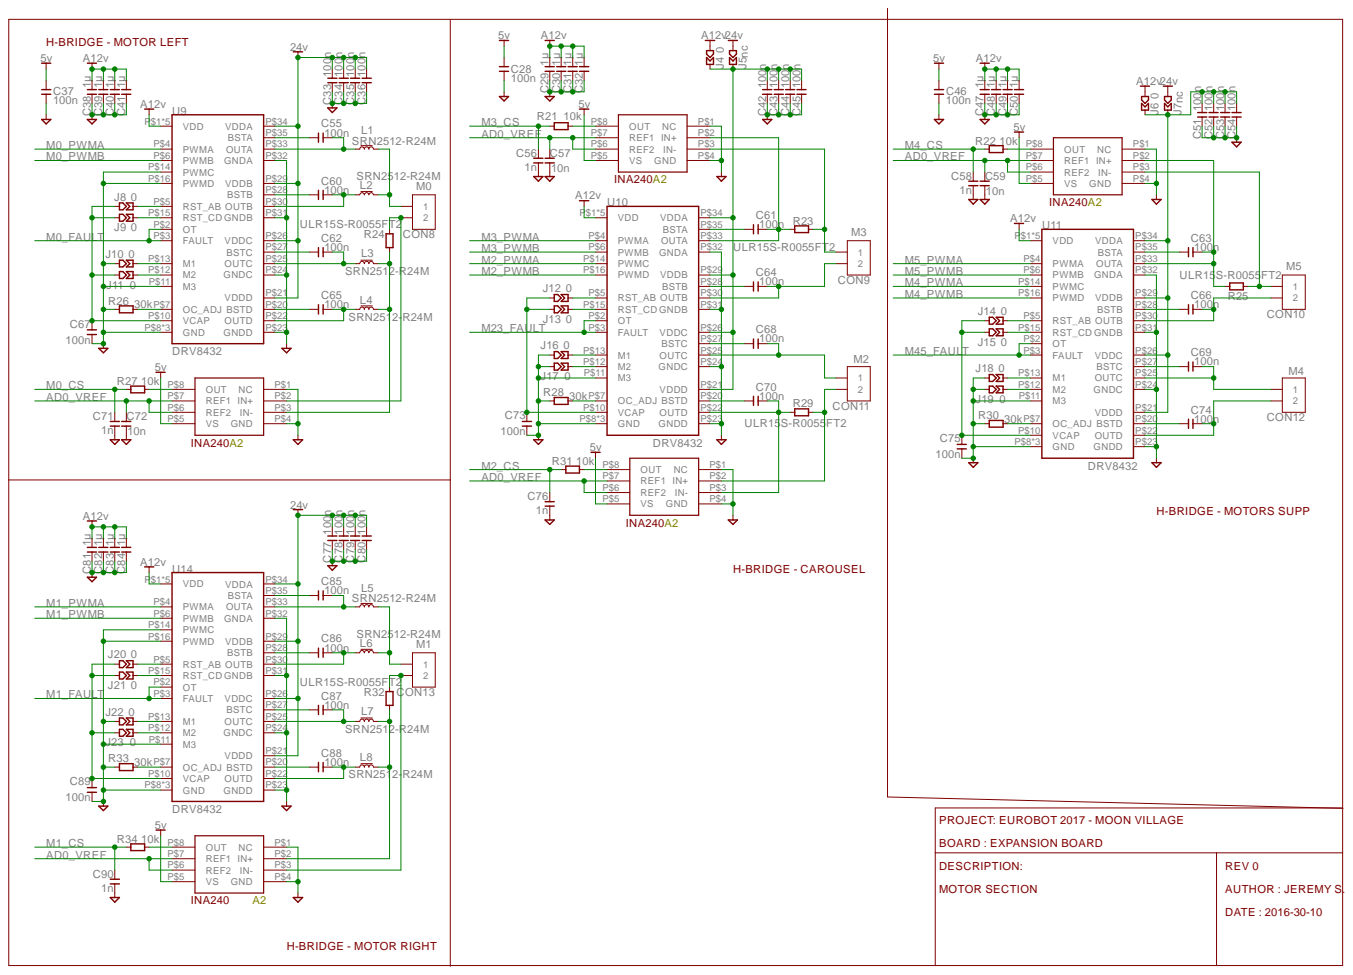
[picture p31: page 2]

PROJECT: EUROBOT 2017 - MOON VILLAGE
BOARD : EXPANSION BOARD
DESCRIPTION:
MOTOR SECTION

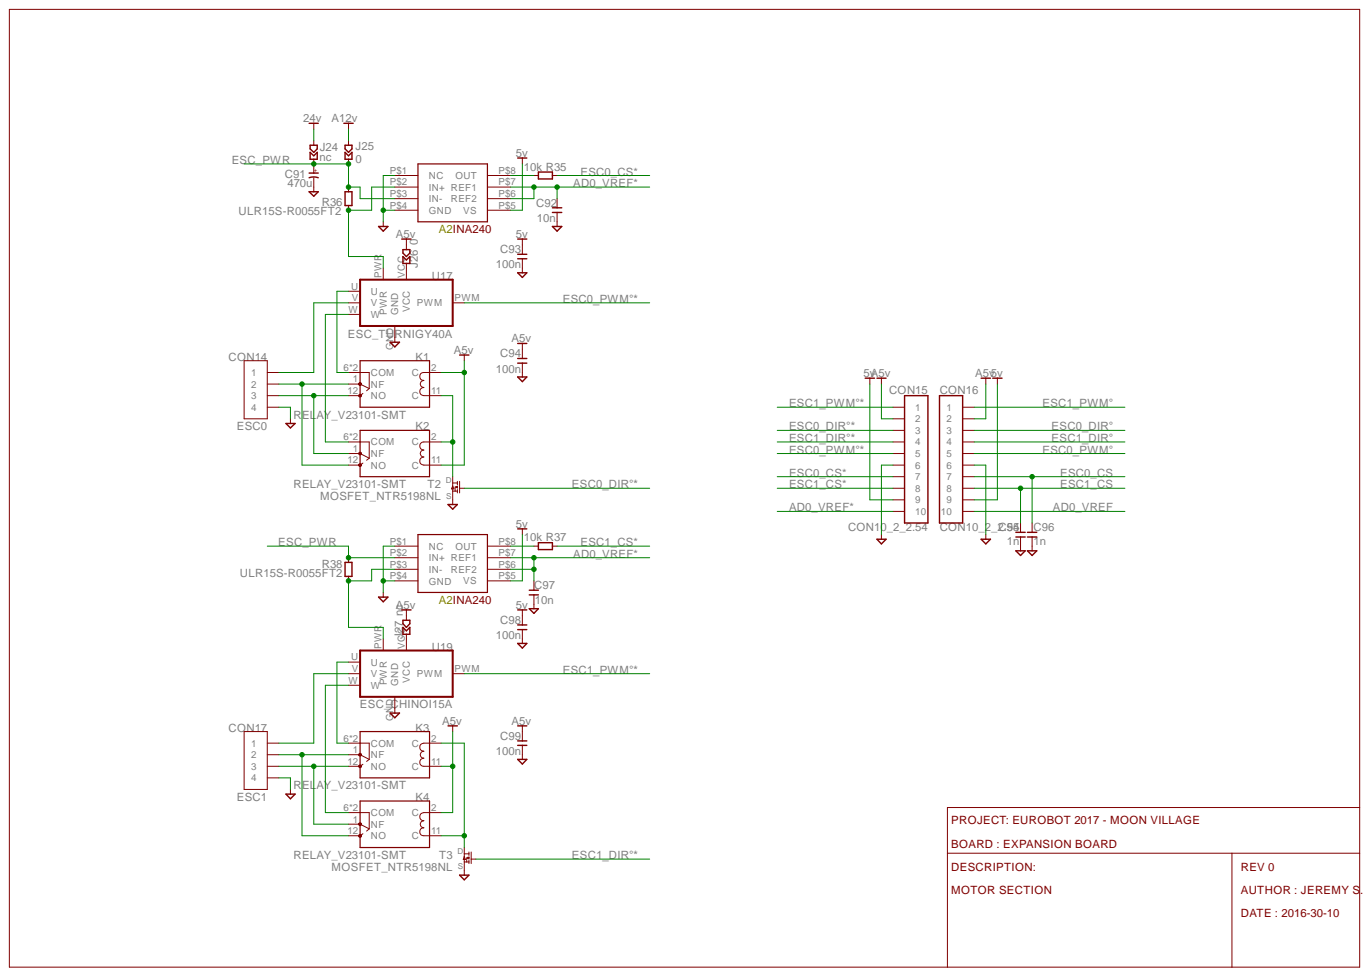
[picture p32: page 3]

PROJECT: EUROBOT 2017 - MOON VILLAGE
BOARD : EXPANSION BOARD
DESCRIPTION:
MOTOR SECTION

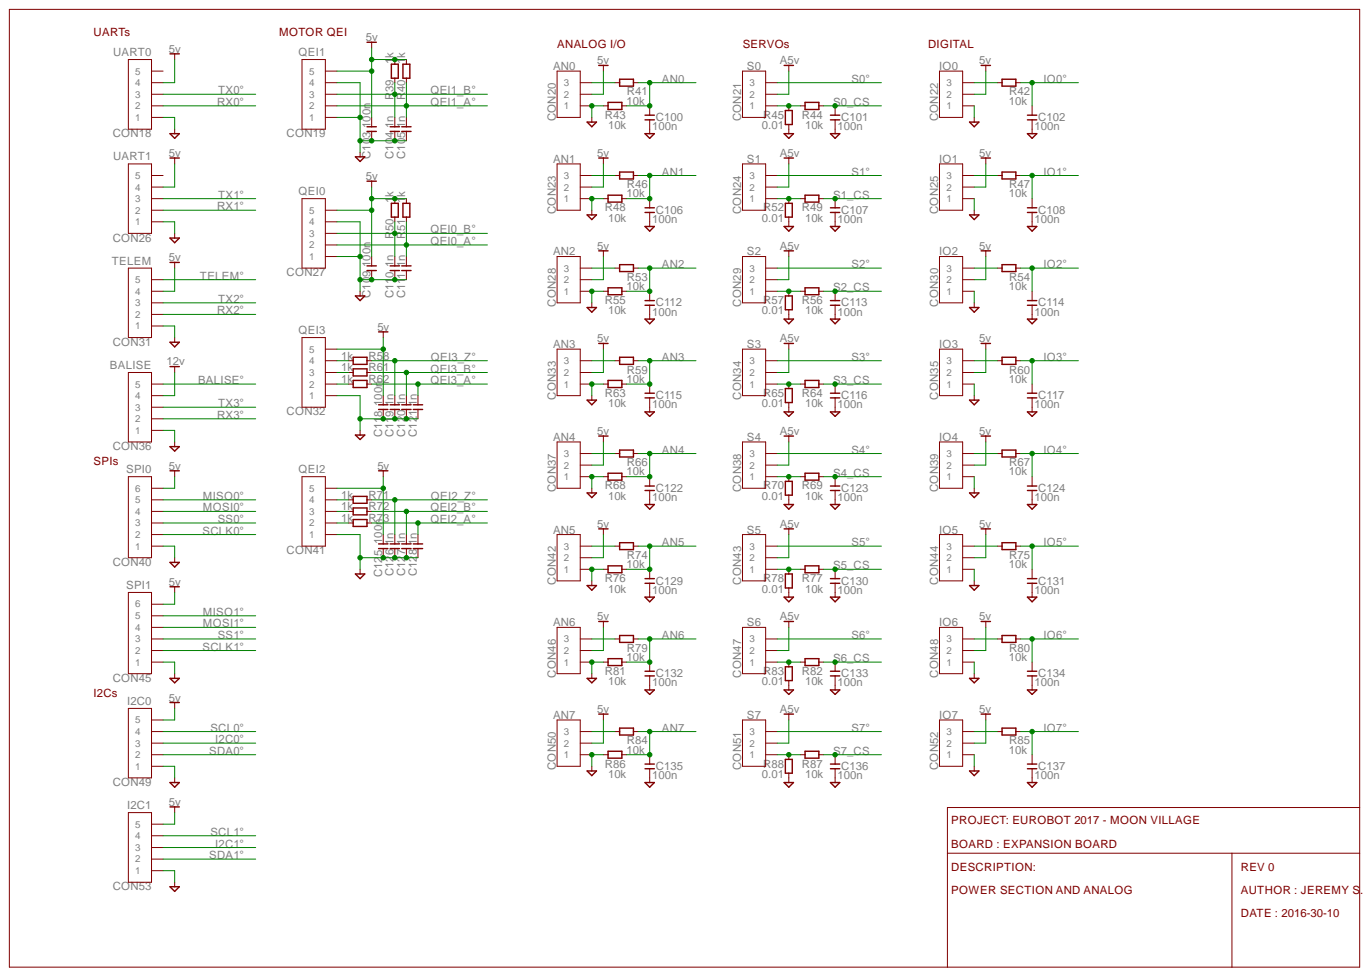
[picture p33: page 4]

PROJECT: EUROBOT 2017 - MOON VILLAGE
BOARD : EXPANSION BOARD
DESCRIPTION:
POWER SECTION AND ANALOG

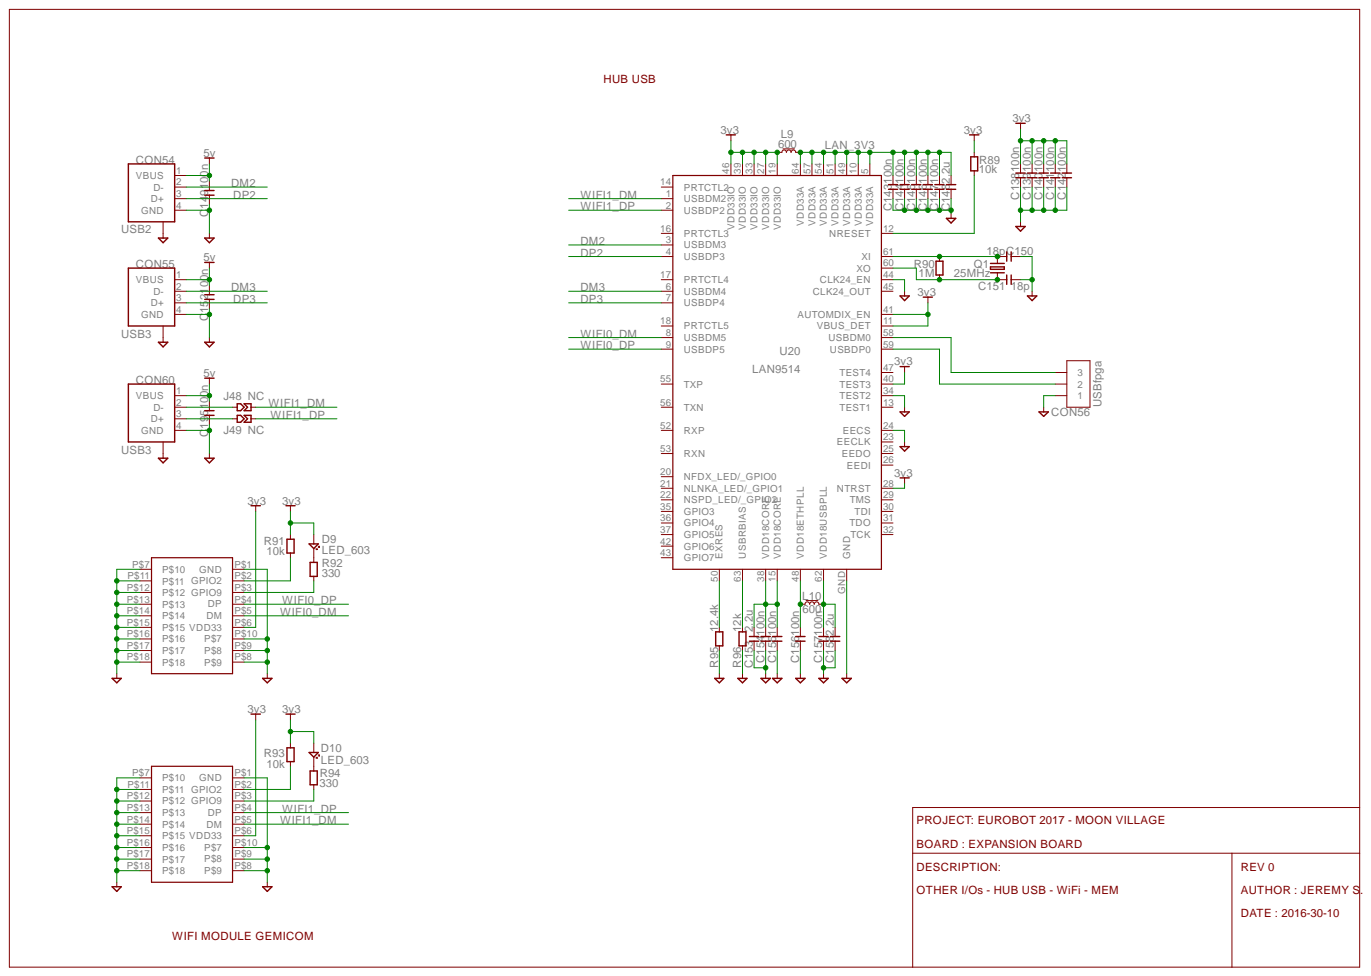
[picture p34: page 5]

PROJECT: EUROBOT 2017 - MOON VILLAGE
BOARD : EXPANSION BOARD
DESCRIPTION:
OTHER I/Os - HUB USB - WiFi - MEM

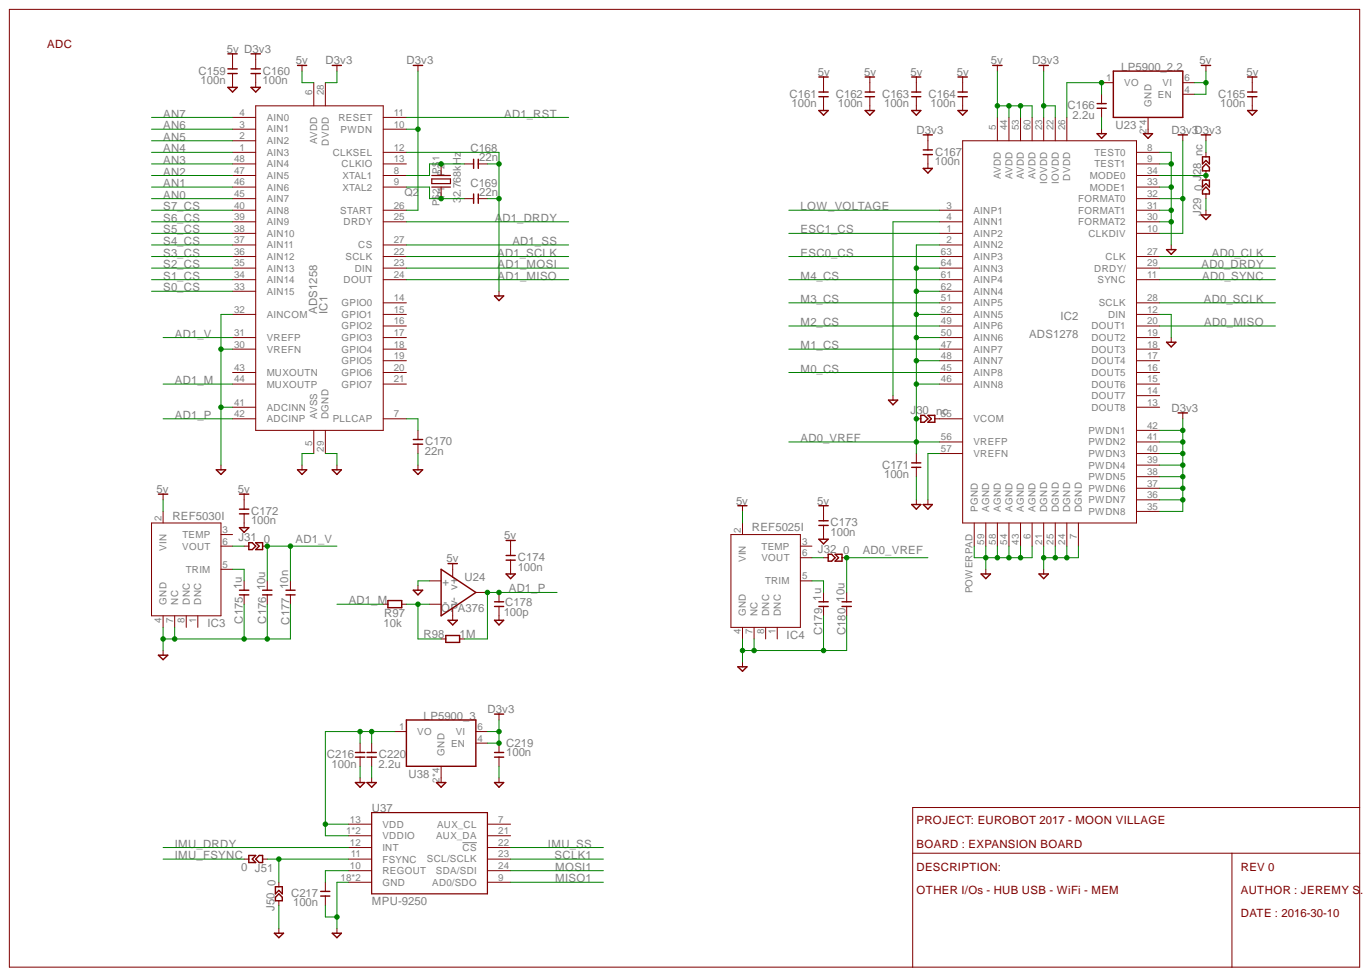
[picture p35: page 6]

PROJECT: EUROBOT 2017 - MOON VILLAGE
BOARD : EXPANSION BOARD
DESCRIPTION:
OTHER I/Os - HUB USB - WiFi - MEM

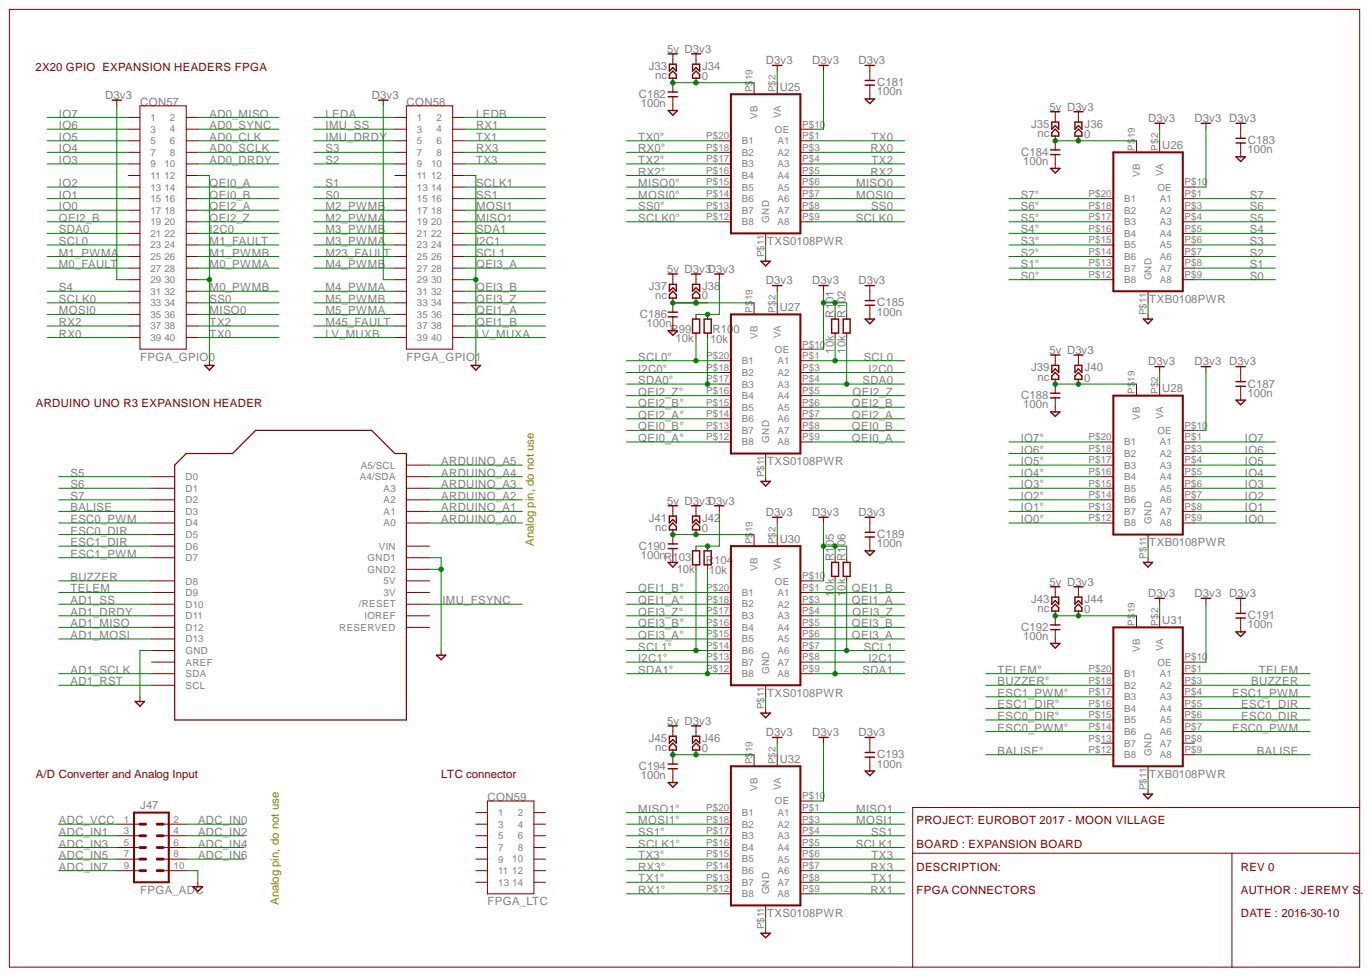
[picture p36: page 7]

2X20 GPIO EXPANSION HEADERS FPGA

ARDUINO UNO R3 EXPANSION HEADER

Analog pin, do not use

PROJECT: EUROBOT 2017 - MOON VILLAGE
BOARD : EXPANSION BOARD
DESCRIPTION:
FPGA CONNECTORS

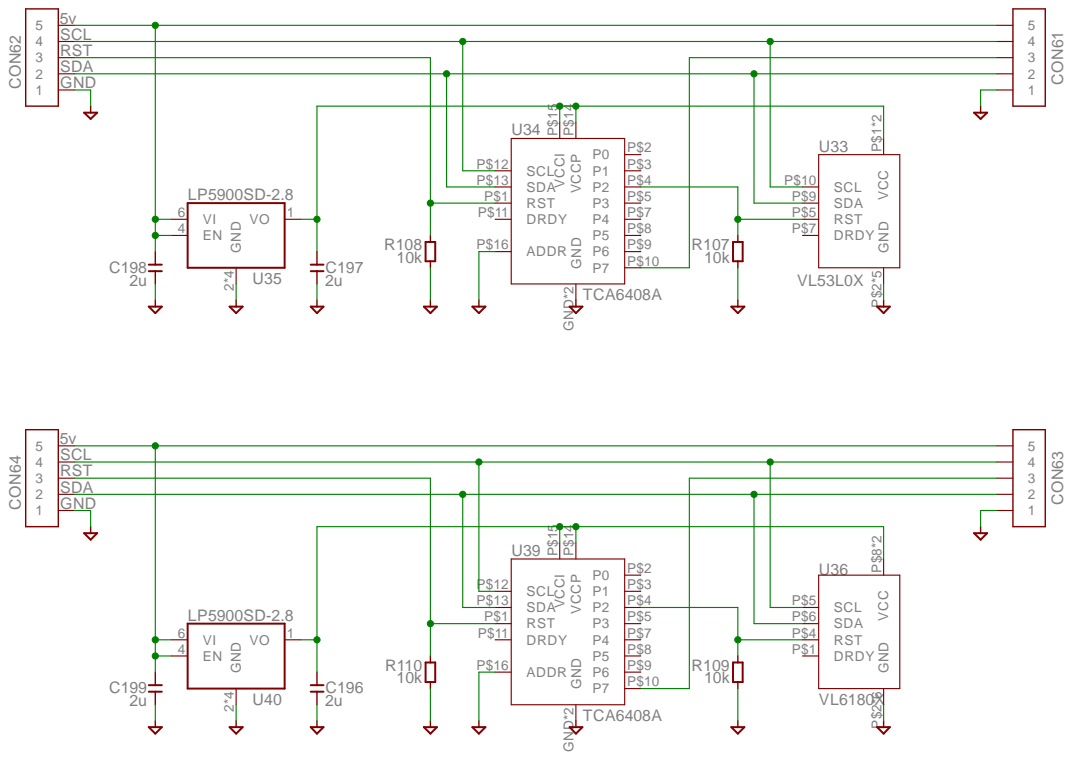
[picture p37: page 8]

SCL
RST
SDA
GND

PROJECT: EUROBOT 2017 - MOON VILLAGE
BOARD : EXPANSION BOARD
DESCRIPTION:
FPGA CONNECTORS

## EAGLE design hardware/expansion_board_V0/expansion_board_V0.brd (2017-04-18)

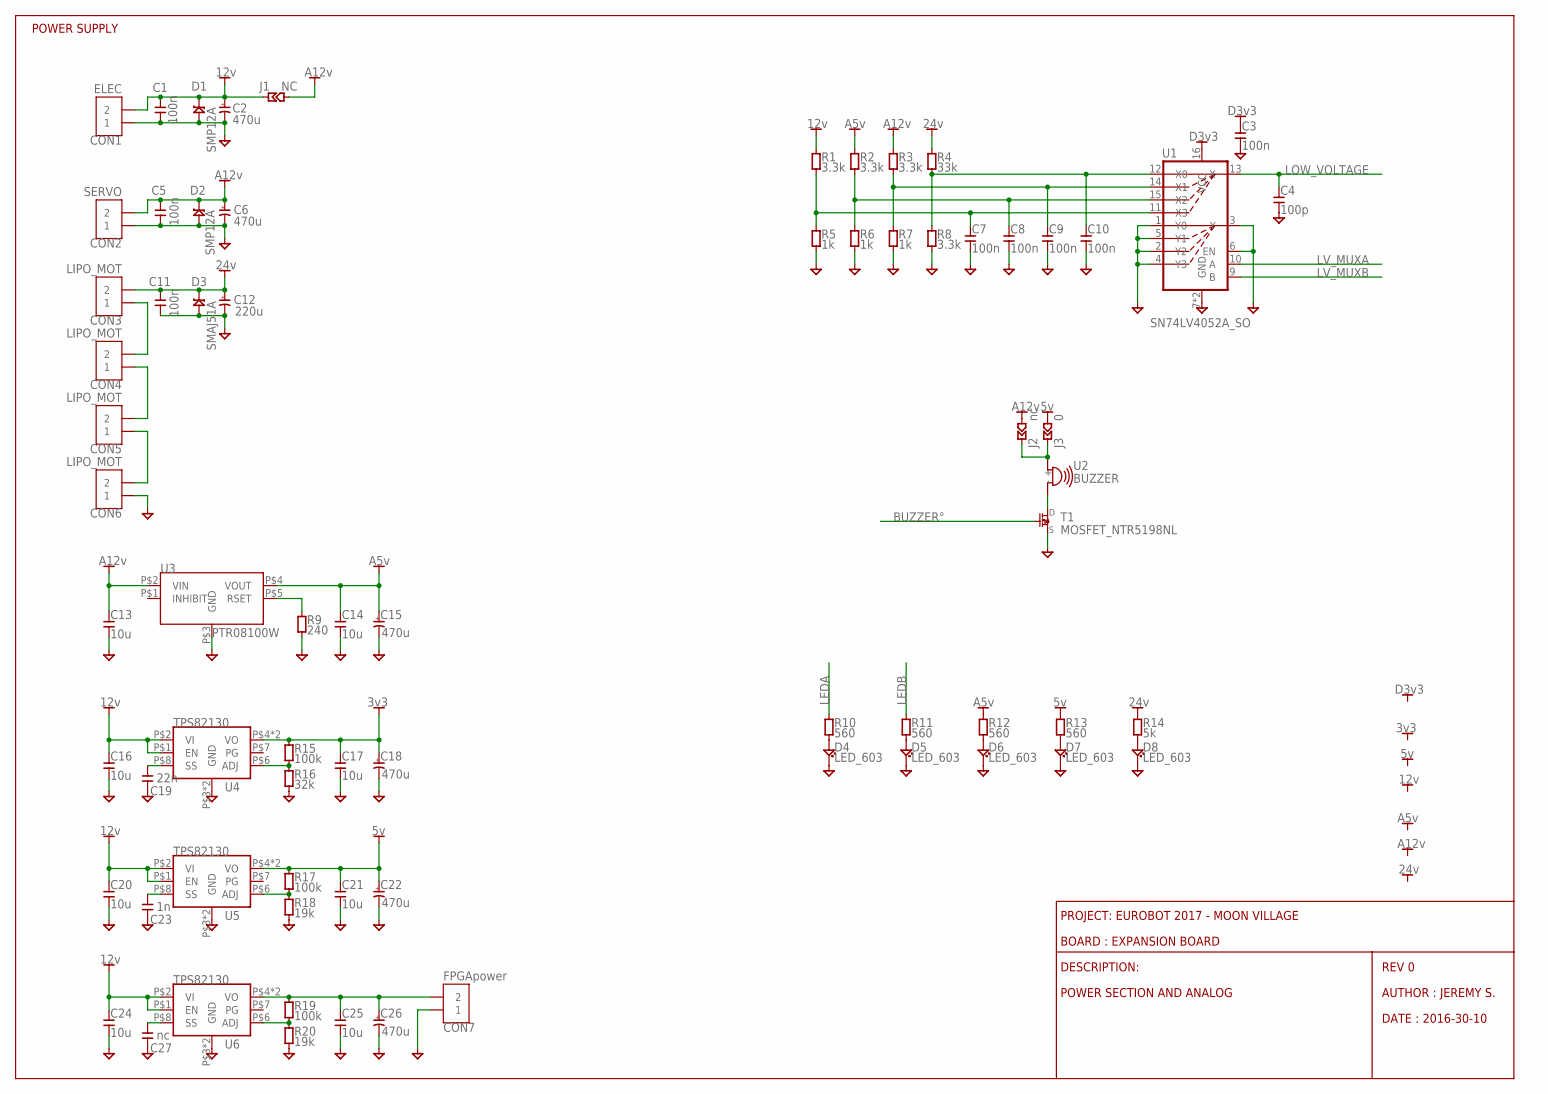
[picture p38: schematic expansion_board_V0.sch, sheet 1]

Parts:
C1, C3, C5, C7, C8, C9, C10: 100n; CAPC1005X55N
C2, C6, C15, C18, C22, C26: 470u; CAPAE835X1020N
C4: 100p; CAPC1005X55N
C11: 100n; CAPC2013X100N
C12: 220u; CAPAE835X1020N
C13, C14, C16, C17, C20, C21, C24, C25: 10u; CAPC2013X100N
C19: 22n; CAPC1005X55N
C23: 1n; CAPC1005X55N
C27: nc; CAPC1005X55N
CON1: ELEC; PHOENIX381P900X920-2N
CON2: SERVO; PHOENIX381P900X920-2N
CON3, CON4, CON5, CON6: LIPO_MOT; PHOENIX381P900X920-2N
CON7: FPGApower; PHOENIX381P900X920-2N
D1, D2: SMP12A; DO220AA
D3: SMAJ51A; D0214AC
D4, D5, D6, D7, D8: LED_603; LEDC1608X60N
J1: NC; JUMC1608X50AN
J2: nc; JUMC1005X50N
J3: 0; JUMC1005X50N
R1, R2, R3, R8: 3.3k; RESC1005X40N
R4: 33k; RESC1005X40N
R5, R6, R7: 1k; RESC1005X40N
R9: 240; RESC1005X40N
R10, R11, R12, R13: 560; RESC1005X40N
R14: 5k; RESC1005X40N
R15, R17, R19: 100k; RESC1005X40N
R16: 32k; RESC1005X40N
R18, R20: 19k; RESC1005X40N
T1: MOSFET_NTR5198NL; SOT95P290X130-3N
U1: SN74LV4052A_SO; SOIC127P780X200-16N
U2: BUZZER; BUZZER_CIRCLE
U3: PTR08100W
U4, U5, U6: TPS82130; SON65P310X290X153-9N

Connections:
3V3: C17.P$1, C18.+, R15.1, U4.P$4 (VO), U4.P$5 (VO); also elsewhere on the board
5V: C21.P$1, C22.+, J3.P$1 (1), R13.1, R17.1, U5.P$4 (VO), U5.P$5 (VO); also elsewhere on the board
12V: C1.1, C2.+, C16.P$1, C20.P$1, C24.P$1, CON1.P$2 (2), D1.C, J1.P$2 (2), R1.1, U4.P$1 (EN), U4.P$2 (VI), U5.P$1 (EN), U5.P$2 (VI), U6.P$1 (EN), U6.P$2 (VI); also elsewhere on the board
24V: C11.P$1, C12.+, CON3.P$2 (2), D3.C, R4.1, R14.1; also elsewhere on the board
A5V: C14.P$1, C15.+, R2.1, R12.1, U3.P$4 (VOUT); also elsewhere on the board
A12V: C5.1, C6.+, C13.P$1, CON2.P$2 (2), D2.C, J1.P$1 (1), J2.P$1 (1), R3.1, U3.P$2 (VIN); also elsewhere on the board
BUZZER°: T1.P$1 (G); also elsewhere on the board
D3V3: C3.1, U1.16 (VCC); also elsewhere on the board
GND: C1.2, C2.-, C3.2, C4.2, C5.2, C6.-, C7.2, C8.2, C9.2, C10.2, C11.P$2, C12.-, C13.P$2, C14.P$2, C15.-, C16.P$2, C17.P$2, C18.-, C19.2, C20.P$2, C21.P$2, C22.-, C23.2, C24.P$2, C25.P$2, C26.-, C27.2, CON1.P$1 (1), CON2.P$1 (1), CON6.P$1 (1), CON7.P$1 (1), D1.A, D2.A, D3.A, D4.C, D5.C, D6.C, D7.C, D8.C, R5.2, R6.2, R7.2, R8.2, R9.2, R16.2, R18.2, R20.2, T1.P$2 (S), U1.1 (Y0), U1.2 (Y2), U1.3 (Y), U1.4 (Y3), U1.5 (Y1), U1.6 (EN), U1.7 (GND), U1.8 (GND), U3.P$3 (GND), U4.P$3 (GND), U4.P$9 (GND), U5.P$3 (GND), U5.P$9 (GND), U6.P$3 (GND), U6.P$9 (GND); also elsewhere on the board
LEDA: R10.1; also elsewhere on the board
LEDB: R11.1; also elsewhere on the board
LOW_VOLTAGE: C4.1, U1.13 (X); also elsewhere on the board
LV_MUXA: U1.10 (A); also elsewhere on the board
LV_MUXB: U1.9 (B); also elsewhere on the board
unnamed: CON3.P$1 (1), CON4.P$2 (2)
unnamed: CON4.P$1 (1), CON5.P$2 (2)
unnamed: CON5.P$1 (1), CON6.P$2 (2)
unnamed: D6.A, R12.2
unnamed: R15.2, R16.1, U4.P$6 (ADJ)
unnamed: D5.A, R11.2
unnamed: D4.A, R10.2
unnamed: C19.1, U4.P$8 (SS)
unnamed: R17.2, R18.1, U5.P$6 (ADJ)
unnamed: C23.1, U5.P$8 (SS)
unnamed: R9.1, U3.P$5 (RSET)
unnamed: R19.2, R20.1, U6.P$6 (ADJ)
unnamed: C27.1, U6.P$8 (SS)
unnamed: D7.A, R13.2
unnamed: D8.A, R14.2
unnamed: C25.P$1, C26.+, CON7.P$2 (2), R19.1, U6.P$4 (VO), U6.P$5 (VO)
unnamed: C7.1, R1.2, R5.1, U1.11 (X3)
unnamed: C10.1, R4.2, R8.1, U1.12 (X0)
unnamed: C8.1, R2.2, R6.1, U1.15 (X2)
unnamed: C9.1, R3.2, R7.1, U1.14 (X1)
unnamed: T1.P$3 (D), U2.-
unnamed: J2.P$2 (2), J3.P$2 (2), U2.+

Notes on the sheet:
REV 0
AUTHOR : JEREMY S.
DATE : 2016-30-10
DESCRIPTION:
BOARD : EXPANSION BOARD
PROJECT: EUROBOT 2017 - MOON VILLAGE
POWER SECTION AND ANALOG
POWER SUPPLY

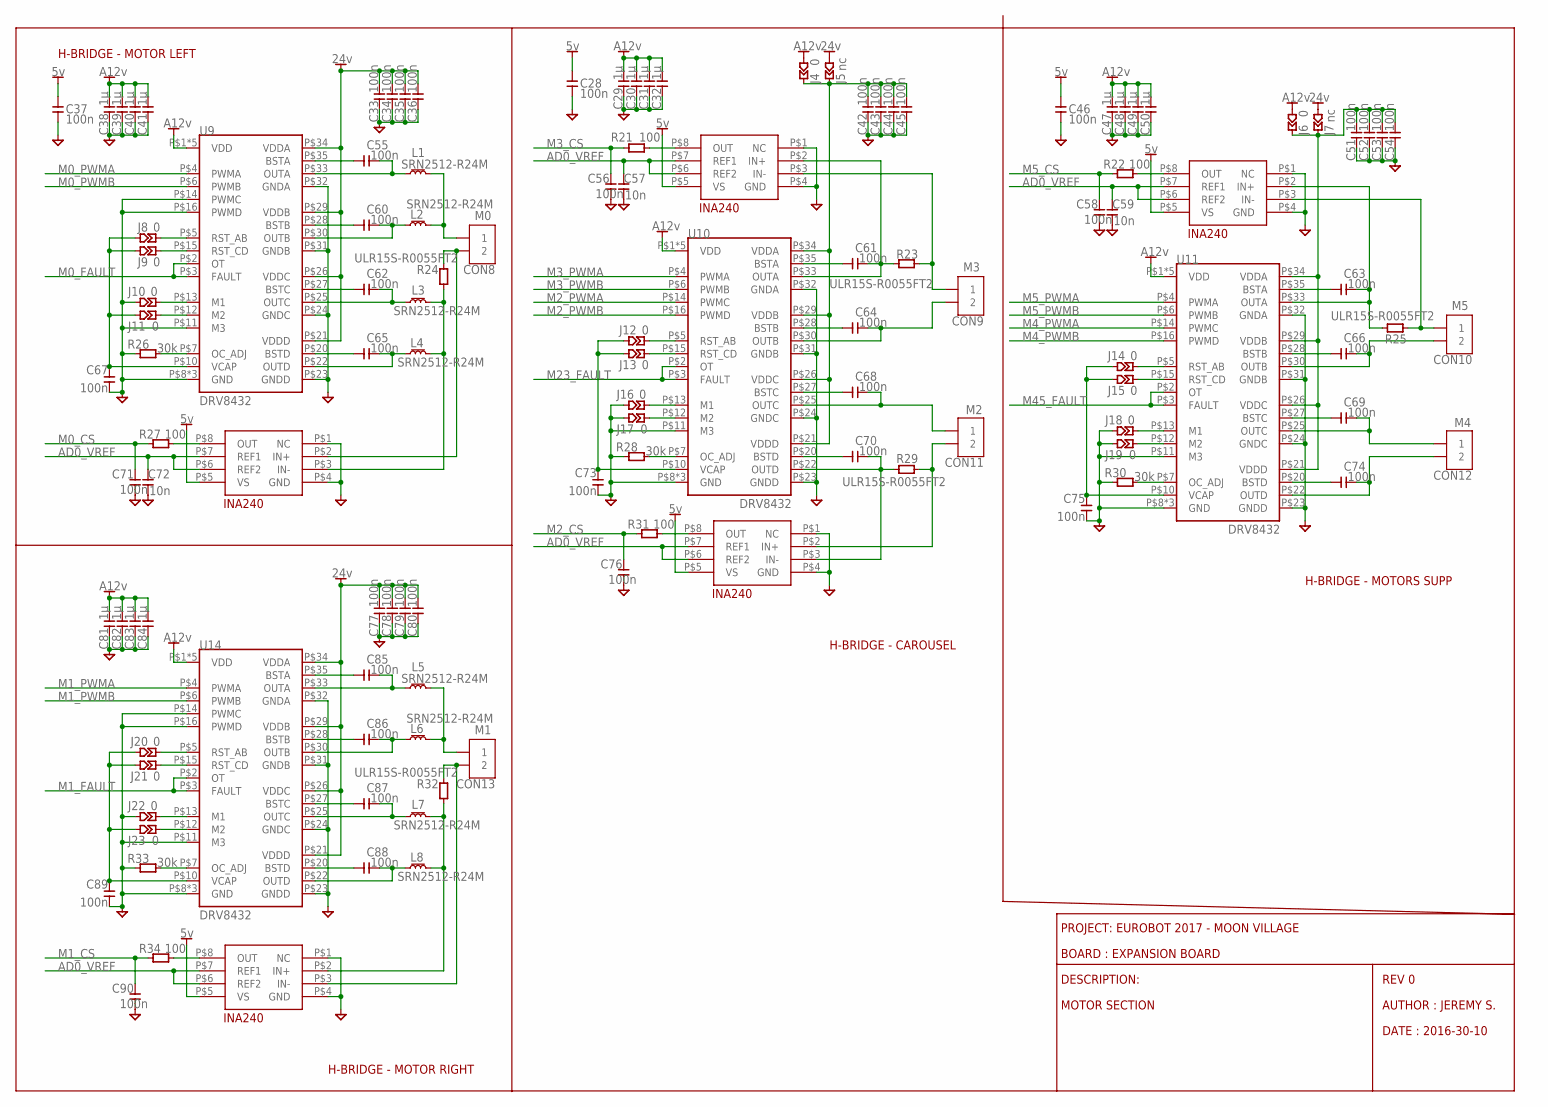
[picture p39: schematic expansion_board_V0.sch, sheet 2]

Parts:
C28, C37, C46, C56, C58, C67, C71, C73, C75, C76, C89, C90: 100n; CAPC1005X55N
C29, C30, C31, C32, C38, C39, C40, C41, C47, C48, C49, C50, C81, C82, C83, C84: 1µ; CAPC1608X95N
C33, C34, C35, C36, C42, C43, C44, C45, C51, C52, C53, C54, C55, C60, C61, C62, C63, C64, C65, C66, C68, C69, C70, C74, C77, C78, C79, C80, C85, C86, C87, C88: 100n; CAPC1608X95N
C57, C59, C72: 10n; CAPC1005X55N
CON8: M0; PHOENIX381P900X920-2N
CON9: M3; PHOENIX381P900X920-2N
CON10: M5; PHOENIX381P900X920-2N
CON11: M2; PHOENIX381P900X920-2N
CON12: M4; PHOENIX381P900X920-2N
CON13: M1; PHOENIX381P900X920-2N
J4, J6: 0; JUMC1608X50AN
J5, J7: nc; JUMC1608X50AN
J8, J9, J10, J11, J12, J13, J14, J15, J16, J17, J18, J19, J20, J21, J22, J23: 0; JUMC1005X50N
L1, L2, L3, L4, L5, L6, L7, L8: SRN2512-R24M; INDC2520X120N
R21, R22, R27, R31, R34: 100; RESC1005X40N
R23, R24, R25, R29, R32: ULR15S-R0055FT2; RESC_ULR15S-R0055FT2
R26, R28, R30, R33: 30k; RESC1005X40N
U7, U8, U12, U13, U15: INA240-A2; TSSOP
U9, U10, U11, U14: DRV8432; R-PDSO-G36

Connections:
5V: C28.2, C37.2, C46.2, U7.P$5 (VS), U8.P$5 (VS), U12.P$5 (VS), U13.P$5 (VS), U15.P$5 (VS); also elsewhere on the board
24V: C33.P$2, C34.P$2, C35.P$2, C36.P$2, C77.P$2, C78.P$2, C79.P$2, C80.P$2, J5.P$1 (1), J7.P$1 (1), U9.P$21 (VDDD), U9.P$26 (VDDC), U9.P$29 (VDDB), U9.P$34 (VDDA), U14.P$21 (VDDD), U14.P$26 (VDDC), U14.P$29 (VDDB), U14.P$34 (VDDA); also elsewhere on the board
A12V: C29.P$2, C30.P$2, C31.P$2, C32.P$2, C38.P$2, C39.P$2, C40.P$2, C41.P$2, C47.P$2, C48.P$2, C49.P$2, C50.P$2, C81.P$2, C82.P$2, C83.P$2, C84.P$2, J4.P$1 (1), J6.P$1 (1), U9.P$1 (VDD), U9.P$17 (VDD), U9.P$18 (VDD), U9.P$19 (VDD), U9.P$36 (VDD), U10.P$1 (VDD), U10.P$17 (VDD), U10.P$18 (VDD), U10.P$19 (VDD), U10.P$36 (VDD), U11.P$1 (VDD), U11.P$17 (VDD), U11.P$18 (VDD), U11.P$19 (VDD), U11.P$36 (VDD), U14.P$1 (VDD), U14.P$17 (VDD), U14.P$18 (VDD), U14.P$19 (VDD), U14.P$36 (VDD); also elsewhere on the board
AD0_VREF: C57.2, C59.2, C72.2, U7.P$6 (REF2), U7.P$7 (REF1), U8.P$6 (REF2), U8.P$7 (REF1), U12.P$6 (REF2), U12.P$7 (REF1), U13.P$6 (REF2), U13.P$7 (REF1), U15.P$6 (REF2), U15.P$7 (REF1); also elsewhere on the board
GND: C28.1, C29.P$1, C30.P$1, C31.P$1, C32.P$1, C33.P$1, C34.P$1, C35.P$1, C36.P$1, C37.1, C38.P$1, C39.P$1, C40.P$1, C41.P$1, C42.P$1, C43.P$1, C44.P$1, C45.P$1, C46.1, C47.P$1, C48.P$1, C49.P$1, C50.P$1, C51.P$1, C52.P$1, C53.P$1, C54.P$1, C56.1, C57.1, C58.1, C59.1, C67.1, C71.1, C72.1, C73.1, C75.1, C76.1, C77.P$1, C78.P$1, C79.P$1, C80.P$1, C81.P$1, C82.P$1, C83.P$1, C84.P$1, C89.1, C90.1, J10.P$1 (1), J16.P$1 (1), J17.P$1 (1), J18.P$1 (1), J19.P$1 (1), J22.P$1 (1), R26.2, R28.2, R30.2, R33.2, U7.P$1 (NC), U7.P$4 (GND), U8.P$1 (NC), U8.P$4 (GND), U9.P$8 (GND), U9.P$9 (GND), U9.P$11 (M3), U9.P$14 (PWMC), U9.P$16 (PWMD), U9.P$23 (GNDD), U9.P$24 (GNDC), U9.P$31 (GNDB), U9.P$32 (GNDA), U9.P$37 (GND), U10.P$8 (GND), U10.P$9 (GND), U10.P$11 (M3), U10.P$23 (GNDD), U10.P$24 (GNDC), U10.P$31 (GNDB), U10.P$32 (GNDA), U10.P$37 (GND), U11.P$8 (GND), U11.P$9 (GND), U11.P$11 (M3), U11.P$23 (GNDD), U11.P$24 (GNDC), U11.P$31 (GNDB), U11.P$32 (GNDA), U11.P$37 (GND), U12.P$1 (NC), U12.P$4 (GND), U13.P$1 (NC), U13.P$4 (GND), U14.P$8 (GND), U14.P$9 (GND), U14.P$11 (M3), U14.P$14 (PWMC), U14.P$16 (PWMD), U14.P$23 (GNDD), U14.P$24 (GNDC), U14.P$31 (GNDB), U14.P$32 (GNDA), U14.P$37 (GND), U15.P$1 (NC), U15.P$4 (GND); also elsewhere on the board
M0_CS: C71.2, R27.2; also elsewhere on the board
M0_FAULT: U9.P$2 (OT), U9.P$3 (FAULT); also elsewhere on the board
M0_PWMA: U9.P$4 (PWMA); also elsewhere on the board
M0_PWMB: U9.P$6 (PWMB); also elsewhere on the board
M1_CS: C90.2, R34.2; also elsewhere on the board
M1_FAULT: U14.P$2 (OT), U14.P$3 (FAULT); also elsewhere on the board
M1_PWMA: U14.P$4 (PWMA); also elsewhere on the board
M1_PWMB: U14.P$6 (PWMB); also elsewhere on the board
M2_CS: C76.2, R31.2; also elsewhere on the board
M2_PWMA: U10.P$14 (PWMC); also elsewhere on the board
M2_PWMB: U10.P$16 (PWMD); also elsewhere on the board
M3_CS: C56.2, R21.2; also elsewhere on the board
M3_PWMA: U10.P$4 (PWMA); also elsewhere on the board
M3_PWMB: U10.P$6 (PWMB); also elsewhere on the board
M4_PWMA: U11.P$14 (PWMC); also elsewhere on the board
M4_PWMB: U11.P$16 (PWMD); also elsewhere on the board
M5_CS: C58.2, R22.2; also elsewhere on the board
M5_PWMA: U11.P$4 (PWMA); also elsewhere on the board
M5_PWMB: U11.P$6 (PWMB); also elsewhere on the board
M23_FAULT: U10.P$2 (OT), U10.P$3 (FAULT); also elsewhere on the board
M45_FAULT: U11.P$2 (OT), U11.P$3 (FAULT); also elsewhere on the board
unnamed: J13.P$2 (2), U10.P$15 (RST_CD)
unnamed: C61.P$1, U10.P$35 (BSTA)
unnamed: C70.P$1, U10.P$20 (BSTD)
unnamed: CON8.P$2 (2), R24.P$2, U12.P$2 (IN+)
unnamed: C68.P$1, U10.P$27 (BSTC)
unnamed: CON13.P$2 (2), R32.P$2, U15.P$3 (IN-)
unnamed: C64.P$1, U10.P$28 (BSTB)
unnamed: CON10.P$1 (1), R25.P$2, U8.P$3 (IN-)
unnamed: C61.P$2, R23.P$1, U7.P$2 (IN+), U10.P$33 (OUTA)
unnamed: C74.P$2, CON12.P$2 (2), U11.P$22 (OUTD)
unnamed: C64.P$2, CON9.P$2 (2), U10.P$30 (OUTB)
unnamed: J20.P$2 (2), U14.P$5 (RST_AB)
unnamed: J16.P$2 (2), U10.P$13 (M1)
unnamed: J8.P$2 (2), U9.P$5 (RST_AB)
unnamed: J12.P$2 (2), U10.P$5 (RST_AB)
unnamed: J14.P$2 (2), U11.P$5 (RST_AB)
unnamed: J17.P$2 (2), U10.P$12 (M2)
unnamed: C68.P$2, CON11.P$1 (1), U10.P$25 (OUTC)
unnamed: C70.P$2, R29.P$1, U10.P$22 (OUTD), U13.P$3 (IN-)
unnamed: C73.2, J12.P$1 (1), J13.P$1 (1), U10.P$10 (VCAP)
unnamed: CON9.P$1 (1), R23.P$2, U7.P$3 (IN-)
unnamed: R28.1, U10.P$7 (OC_ADJ)
unnamed: R21.1, U7.P$8 (OUT)
unnamed: CON11.P$2 (2), R29.P$2, U13.P$2 (IN+)
unnamed: C63.P$1, U11.P$35 (BSTA)
unnamed: C74.P$1, U11.P$20 (BSTD)
unnamed: C69.P$1, U11.P$27 (BSTC)
unnamed: C66.P$1, U11.P$28 (BSTB)
unnamed: C63.P$2, R25.P$1, U8.P$2 (IN+), U11.P$33 (OUTA)
unnamed: C66.P$2, CON10.P$2 (2), U11.P$30 (OUTB)
unnamed: C69.P$2, CON12.P$1 (1), U11.P$25 (OUTC)
unnamed: C75.2, J14.P$1 (1), J15.P$1 (1), U11.P$10 (VCAP)
unnamed: R30.1, U11.P$7 (OC_ADJ)
unnamed: C42.P$2, C43.P$2, C44.P$2, C45.P$2, J4.P$2 (2), J5.P$2 (2), U10.P$21 (VDDD), U10.P$26 (VDDC), U10.P$29 (VDDB), U10.P$34 (VDDA)
unnamed: J15.P$2 (2), U11.P$15 (RST_CD)
unnamed: R31.1, U13.P$8 (OUT)
unnamed: J18.P$2 (2), U11.P$13 (M1)
unnamed: J19.P$2 (2), U11.P$12 (M2)
unnamed: C51.P$2, C52.P$2, C53.P$2, C54.P$2, J6.P$2 (2), J7.P$2 (2), U11.P$21 (VDDD), U11.P$26 (VDDC), U11.P$29 (VDDB), U11.P$34 (VDDA)
unnamed: C85.P$1, U14.P$35 (BSTA)
unnamed: C88.P$1, U14.P$20 (BSTD)
unnamed: C87.P$1, U14.P$27 (BSTC)
unnamed: C86.P$1, U14.P$28 (BSTB)
unnamed: C85.P$2, L5.P$2 (2), U14.P$33 (OUTA)
unnamed: C86.P$2, L6.P$2 (2), U14.P$30 (OUTB)
unnamed: C87.P$2, L7.P$2 (2), U14.P$25 (OUTC)
unnamed: C88.P$2, L8.P$2 (2), U14.P$22 (OUTD)
unnamed: C89.2, J20.P$1 (1), J21.P$1 (1), J23.P$1 (1), U14.P$10 (VCAP)
unnamed: R33.1, U14.P$7 (OC_ADJ)
unnamed: C55.P$1, U9.P$35 (BSTA)
unnamed: J21.P$2 (2), U14.P$15 (RST_CD)
unnamed: J22.P$2 (2), U14.P$13 (M1)
unnamed: J23.P$2 (2), U14.P$12 (M2)
unnamed: C65.P$1, U9.P$20 (BSTD)
unnamed: R34.1, U15.P$8 (OUT)
unnamed: C62.P$1, U9.P$27 (BSTC)
unnamed: L7.P$1 (1), L8.P$1 (1), R32.P$1, U15.P$2 (IN+)
unnamed: C60.P$1, U9.P$28 (BSTB)
unnamed: CON13.P$1 (1), L5.P$1 (1), L6.P$1 (1)
unnamed: C55.P$2, L1.P$2 (2), U9.P$33 (OUTA)
unnamed: C60.P$2, L2.P$2 (2), U9.P$30 (OUTB)
unnamed: C62.P$2, L3.P$2 (2), U9.P$25 (OUTC)
unnamed: C65.P$2, L4.P$2 (2), U9.P$22 (OUTD)
unnamed: C67.2, J8.P$1 (1), J9.P$1 (1), J11.P$1 (1), U9.P$10 (VCAP)
unnamed: R26.1, U9.P$7 (OC_ADJ)
unnamed: J9.P$2 (2), U9.P$15 (RST_CD)
unnamed: J10.P$2 (2), U9.P$13 (M1)
unnamed: J11.P$2 (2), U9.P$12 (M2)
unnamed: R27.1, U12.P$8 (OUT)
unnamed: L3.P$1 (1), L4.P$1 (1), R24.P$1, U12.P$3 (IN-)
unnamed: CON8.P$1 (1), L1.P$1 (1), L2.P$1 (1)
unnamed: R22.1, U8.P$8 (OUT)

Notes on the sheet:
REV 0
AUTHOR : JEREMY S.
DATE : 2016-30-10
DESCRIPTION:
BOARD : EXPANSION BOARD
PROJECT: EUROBOT 2017 - MOON VILLAGE
H-BRIDGE - MOTOR LEFT
MOTOR SECTION
H-BRIDGE - MOTOR RIGHT
H-BRIDGE - CAROUSEL
H-BRIDGE - MOTORS SUPP

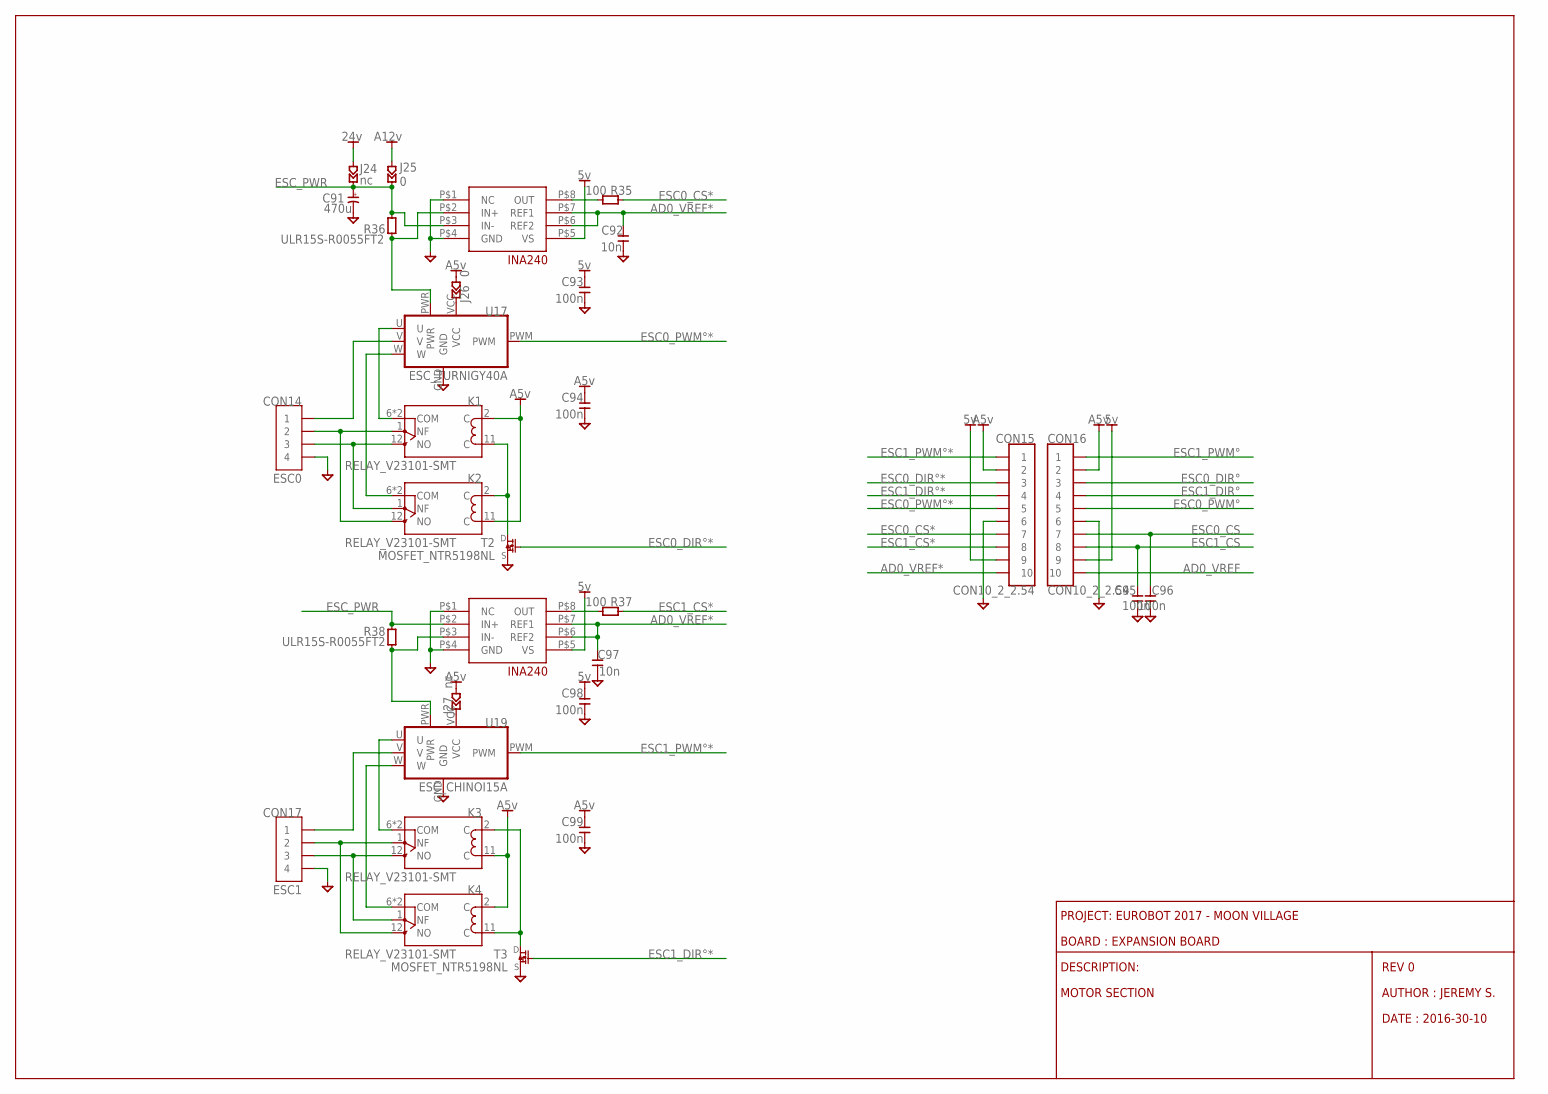
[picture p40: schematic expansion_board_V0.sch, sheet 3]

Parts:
C91: 470u; CAPAE835X1020N
C92, C97: 10n; CAPC1005X55N
C93, C94, C95, C96, C98, C99: 100n; CAPC1005X55N
CON14: ESC0; PHOENIX381P1662X920-4N
CON15, CON16: CON10_2_2.54; CON245P2030X890-2X5N
CON17: ESC1; PHOENIX381P1662X920-4N
J24: nc; JUMC1608X50AN
J25: 0; JUMC1608X50AN
J26: 0; JUMC1005X50N
J27: nc; JUMC1005X50N
K1, K2, K3, K4: RELAY_V23101-SMT; V23101-D0103-A201-SMT
R35, R37: 100; RESC1005X40N
R36, R38: ULR15S-R0055FT2; RESC_ULR15S-R0055FT2
T2, T3: MOSFET_NTR5198NL; SOT95P290X130-3N
U16, U18: INA240-A2; TSSOP
U17: ESC_TURNIGY40A
U19: ESC_CHINOI15A

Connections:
5V: C93.1, C98.1, CON15.P$9 (9), CON16.P$9 (9), U16.P$5 (VS), U18.P$5 (VS); also elsewhere on the board
24V: J24.P$1 (1); also elsewhere on the board
A5V: C94.1, C99.1, CON15.P$2 (2), CON16.P$2 (2), J26.P$1 (1), J27.P$1 (1), K1.2 (C), K2.11 (C), K3.11 (C), K4.2 (C); also elsewhere on the board
A12V: J25.P$1 (1); also elsewhere on the board
AD0_VREF: CON16.P$10 (10); also elsewhere on the board
AD0_VREF*: C92.2, C97.2, CON15.P$10 (10), U16.P$6 (REF2), U16.P$7 (REF1), U18.P$6 (REF2), U18.P$7 (REF1)
ESC0_CS: C96.2, CON16.P$7 (7); also elsewhere on the board
ESC0_CS*: CON15.P$7 (7), R35.2
ESC0_DIR°: CON16.P$3 (3); also elsewhere on the board
ESC0_DIR°*: CON15.P$3 (3), T2.P$1 (G)
ESC0_PWM°: CON16.P$5 (5); also elsewhere on the board
ESC0_PWM°*: CON15.P$5 (5), U17.PWM
ESC1_CS: C95.2, CON16.P$8 (8); also elsewhere on the board
ESC1_CS*: CON15.P$8 (8), R37.2
ESC1_DIR°: CON16.P$4 (4); also elsewhere on the board
ESC1_DIR°*: CON15.P$4 (4), T3.P$1 (G)
ESC1_PWM°: CON16.P$1 (1); also elsewhere on the board
ESC1_PWM°*: CON15.P$1 (1), U19.PWM
ESC_PWR: C91.+, J24.P$2 (2), J25.P$2 (2), R36.P$2, R38.P$2, U16.P$3 (IN-), U18.P$2 (IN+)
GND: C91.-, C92.1, C93.2, C94.2, C95.1, C96.1, C97.1, C98.2, C99.2, CON14.P$4 (4), CON15.P$6 (6), CON16.P$6 (6), CON17.P$4 (4), T2.P$2 (S), T3.P$2 (S), U16.P$1 (NC), U16.P$4 (GND), U17.GND, U18.P$1 (NC), U18.P$4 (GND), U19.GND; also elsewhere on the board
unnamed: K3.2 (C), K4.11 (C), T3.P$3 (D)
unnamed: K1.11 (C), K2.2 (C), T2.P$3 (D)
unnamed: K2.6 (COM), K2.7 (COM), U17.W
unnamed: K1.6 (COM), K1.7 (COM), U17.U
unnamed: CON14.P$2 (2), K1.1 (NF), K2.12 (NO)
unnamed: CON14.P$3 (3), K1.12 (NO), K2.1 (NF)
unnamed: CON14.P$1 (1), U17.V
unnamed: R35.1, U16.P$8 (OUT)
unnamed: R36.P$1, U16.P$2 (IN+), U17.PWR
unnamed: J27.P$2 (2), U19.VCC
unnamed: J26.P$2 (2), U17.VCC
unnamed: K4.6 (COM), K4.7 (COM), U19.W
unnamed: K3.6 (COM), K3.7 (COM), U19.U
unnamed: CON17.P$2 (2), K3.1 (NF), K4.12 (NO)
unnamed: CON17.P$3 (3), K3.12 (NO), K4.1 (NF)
unnamed: CON17.P$1 (1), U19.V
unnamed: R37.1, U18.P$8 (OUT)
unnamed: R38.P$1, U18.P$3 (IN-), U19.PWR

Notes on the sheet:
REV 0
AUTHOR : JEREMY S.
DATE : 2016-30-10
DESCRIPTION:
BOARD : EXPANSION BOARD
PROJECT: EUROBOT 2017 - MOON VILLAGE
MOTOR SECTION

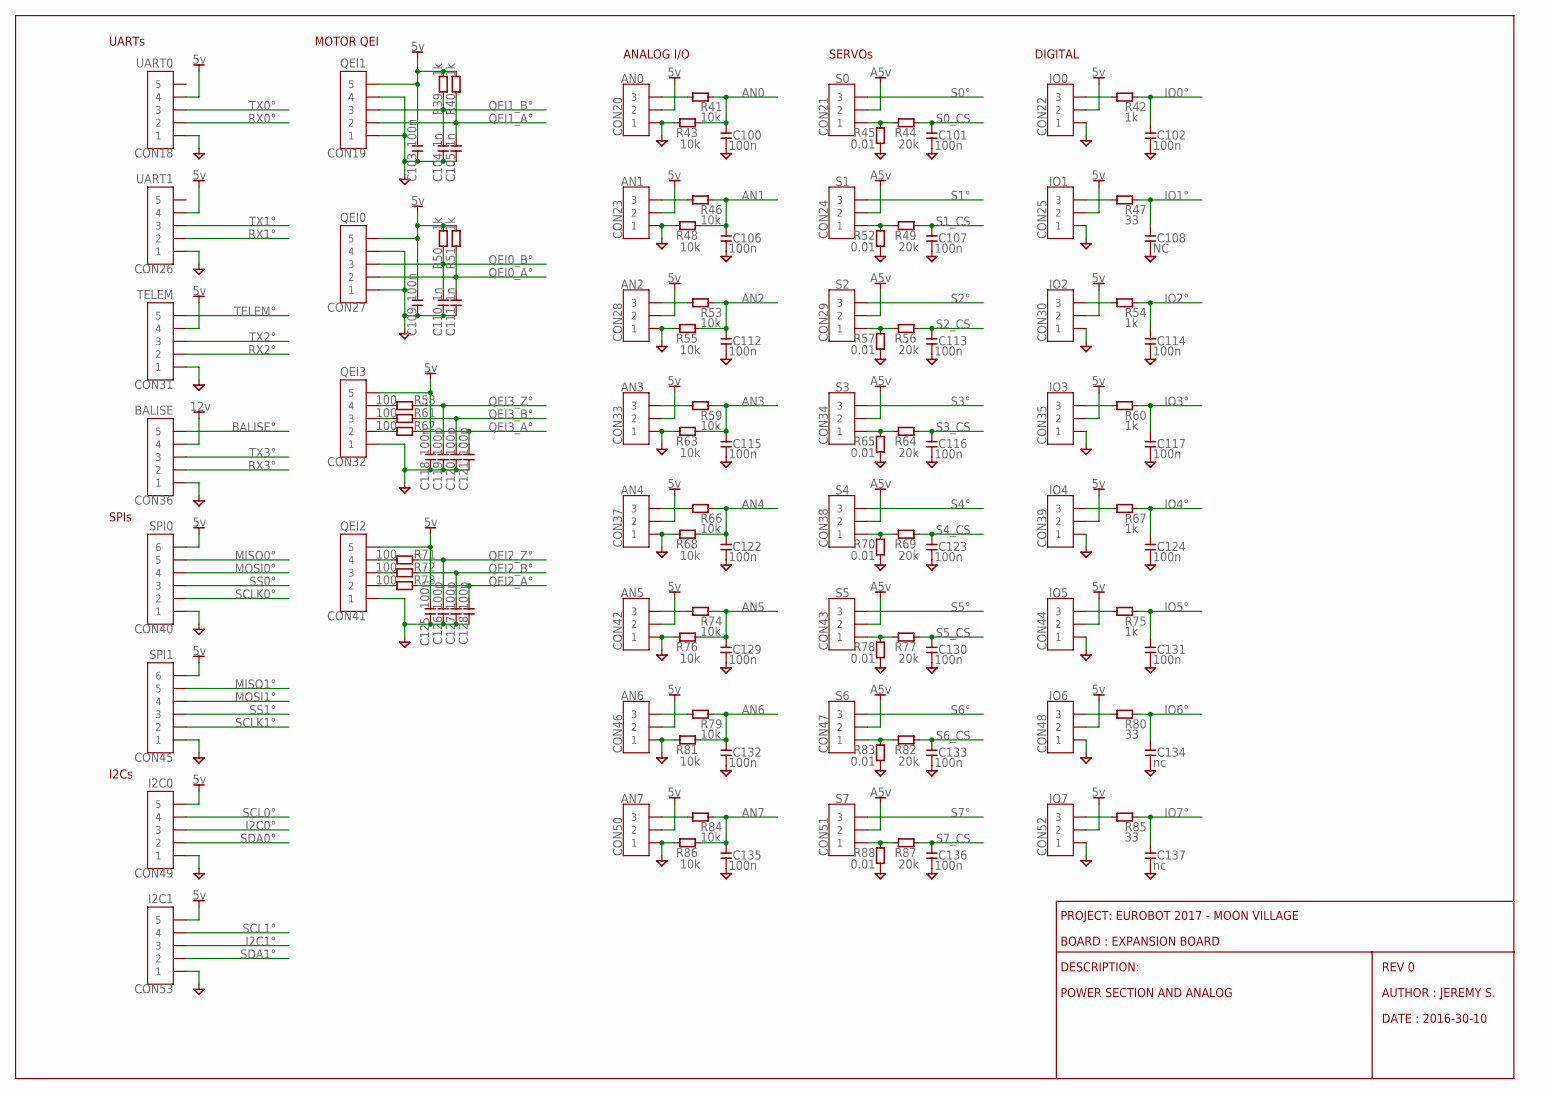
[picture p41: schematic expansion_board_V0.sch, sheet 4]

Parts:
C100, C101, C102, C103, C106, C107, C109, C112, C113, C114, C115, C116, C117, C118, C122, C123, C124, C125, C129, C130, C131, C132, C133, C135, C136: 100n; CAPC1005X55N
C104, C105, C110, C111: 1n; CAPC1005X55N
C108: NC; CAPC1005X55N
C119, C120, C121, C126, C127, C128: 100p; CAPC1005X55N
C134, C137: nc; CAPC1005X55N
CON18: UART0; CON254P1270X400-5S
CON19: QEI1; CON254P1270X400-5S
CON20: AN0; CON254P762X400-3SMT
CON21: S0; CON254P762X400-3SMT
CON22: IO0; CON254P762X400-3SMT
CON23: AN1; CON254P762X400-3SMT
CON24: S1; CON254P762X400-3SMT
CON25: IO1; CON254P762X400-3SMT
CON26: UART1; CON254P1270X400-5S
CON27: QEI0; CON254P1270X400-5S
CON28: AN2; CON254P762X400-3SMT
CON29: S2; CON254P762X400-3SMT
CON30: IO2; CON254P762X400-3SMT
CON31: TELEM; CON254P1270X400-5S
CON32: QEI3; CON254P1270X400-5S
CON33: AN3; CON254P762X400-3SMT
CON34: S3; CON254P762X400-3SMT
CON35: IO3; CON254P762X400-3SMT
CON36: BALISE; CON254P1270X400-5S
CON37: AN4; CON254P762X400-3SMT
CON38: S4; CON254P762X400-3SMT
CON39: IO4; CON254P762X400-3SMT
CON40: SPI0; CON254P1524X400-6N-S
CON41: QEI2; CON254P1270X400-5S
CON42: AN5; CON254P762X400-3SMT
CON43: S5; CON254P762X400-3SMT
CON44: IO5; CON254P762X400-3SMT
CON45: SPI1; CON254P1524X400-6N-S
CON46: AN6; CON254P762X400-3SMT
CON47: S6; CON254P762X400-3SMT
CON48: IO6; CON254P762X400-3SMT
CON49: I2C0; CON254P1270X400-5S
CON50: AN7; CON254P762X400-3SMT
CON51: S7; CON254P762X400-3SMT
CON52: IO7; CON254P762X400-3SMT
CON53: I2C1; CON254P1270X400-5S
R39, R40, R42, R50, R51, R54, R60, R67, R75: 1k; RESC1005X40N
R41, R43, R46, R48, R53, R55, R59, R63, R66, R68, R74, R76, R79, R81, R84, R86: 10k; RESC1005X40N
R44, R49, R56, R64, R69, R77, R82, R87: 20k; RESC1005X40N
R45, R52, R57, R65, R70, R78, R83, R88: 0.01; RESC1608X50AN
R47, R80, R85: 33; RESC1005X40N
R58, R61, R62, R71, R72, R73: 100; RESC1005X40N

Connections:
5V: C103.2, C109.2, C118.2, C125.2, CON18.4, CON19.5, CON20.2, CON22.2, CON23.2, CON25.2, CON26.4, CON27.5, CON28.2, CON30.2, CON31.4, CON32.5, CON33.2, CON35.2, CON37.2, CON39.2, CON40.6, CON41.5, CON42.2, CON44.2, CON45.6, CON46.2, CON48.2, CON49.5, CON50.2, CON52.2, CON53.5, R39.2, R40.2, R50.2, R51.2; also elsewhere on the board
12V: CON36.4; also elsewhere on the board
A5V: CON21.2, CON24.2, CON29.2, CON34.2, CON38.2, CON43.2, CON47.2, CON51.2; also elsewhere on the board
AN0: C100.2, R41.2, R43.1; also elsewhere on the board
AN1: C106.2, R46.2, R48.1; also elsewhere on the board
AN2: C112.2, R53.2, R55.1; also elsewhere on the board
AN3: C115.2, R59.2, R63.1; also elsewhere on the board
AN4: C122.2, R66.2, R68.1; also elsewhere on the board
AN5: C129.2, R74.2, R76.1; also elsewhere on the board
AN6: C132.2, R79.2, R81.1; also elsewhere on the board
AN7: C135.2, R84.2, R86.1; also elsewhere on the board
BALISE°: CON36.5; also elsewhere on the board
GND: C100.1, C101.1, C102.1, C103.1, C104.1, C105.1, C106.1, C107.1, C108.1, C109.1, C110.1, C111.1, C112.1, C113.1, C114.1, C115.1, C116.1, C117.1, C118.1, C119.1, C120.1, C121.1, C122.1, C123.1, C124.1, C125.1, C126.1, C127.1, C128.1, C129.1, C130.1, C131.1, C132.1, C133.1, C134.1, C135.1, C136.1, C137.1, CON18.1, CON19.1, CON19.4, CON20.1, CON22.1, CON23.1, CON25.1, CON26.1, CON27.1, CON27.4, CON28.1, CON30.1, CON31.1, CON32.1, CON33.1, CON35.1, CON36.1, CON37.1, CON39.1, CON40.1, CON41.1, CON42.1, CON44.1, CON45.1, CON46.1, CON48.1, CON49.1, CON50.1, CON52.1, CON53.1, R43.2, R45.P$2, R48.2, R52.P$2, R55.2, R57.P$2, R63.2, R65.P$2, R68.2, R70.P$2, R76.2, R78.P$2, R81.2, R83.P$2, R86.2, R88.P$2; also elsewhere on the board
I2C0°: CON49.3; also elsewhere on the board
I2C1°: CON53.3; also elsewhere on the board
IO0°: C102.2, R42.2; also elsewhere on the board
IO1°: C108.2, R47.2; also elsewhere on the board
IO2°: C114.2, R54.2; also elsewhere on the board
IO3°: C117.2, R60.2; also elsewhere on the board
IO4°: C124.2, R67.2; also elsewhere on the board
IO5°: C131.2, R75.2; also elsewhere on the board
IO6°: C134.2, R80.2; also elsewhere on the board
IO7°: C137.2, R85.2; also elsewhere on the board
MISO0°: CON40.5; also elsewhere on the board
MISO1°: CON45.5; also elsewhere on the board
MOSI0°: CON40.4; also elsewhere on the board
MOSI1°: CON45.4; also elsewhere on the board
unnamed: CON21.1, R44.2, R45.P$1
unnamed: CON24.1, R49.2, R52.P$1
unnamed: CON29.1, R56.2, R57.P$1
unnamed: CON50.3, R84.1
unnamed: CON20.3, R41.1
unnamed: CON23.3, R46.1
unnamed: CON28.3, R53.1
unnamed: CON33.3, R59.1
unnamed: CON37.3, R66.1
unnamed: CON34.1, R64.2, R65.P$1
unnamed: CON38.1, R69.2, R70.P$1
unnamed: CON43.1, R77.2, R78.P$1
unnamed: CON47.1, R82.2, R83.P$1
unnamed: CON51.1, R87.2, R88.P$1
unnamed: CON42.3, R74.1
unnamed: CON46.3, R79.1
unnamed: CON52.3, R85.1
unnamed: CON22.3, R42.1
unnamed: CON25.3, R47.1
unnamed: CON30.3, R54.1
unnamed: CON35.3, R60.1
unnamed: CON39.3, R67.1
unnamed: CON44.3, R75.1
unnamed: CON48.3, R80.1
unnamed: CON41.4, R71.2
unnamed: CON41.3, R72.2
unnamed: CON41.2, R73.2
unnamed: CON32.4, R58.2
unnamed: CON32.3, R61.2
unnamed: CON32.2, R62.2
QEI0_A°: C111.2, CON27.2, R51.1; also elsewhere on the board
QEI0_B°: C110.2, CON27.3, R50.1; also elsewhere on the board
QEI1_A°: C105.2, CON19.2, R40.1; also elsewhere on the board
QEI1_B°: C104.2, CON19.3, R39.1; also elsewhere on the board
QEI2_A°: C128.2, R73.1; also elsewhere on the board
QEI2_B°: C127.2, R72.1; also elsewhere on the board
QEI2_Z°: C126.2, R71.1; also elsewhere on the board
QEI3_A°: C121.2, R62.1; also elsewhere on the board
QEI3_B°: C120.2, R61.1; also elsewhere on the board
QEI3_Z°: C119.2, R58.1; also elsewhere on the board
RX0°: CON18.2; also elsewhere on the board
RX1°: CON26.2; also elsewhere on the board
RX2°: CON31.2; also elsewhere on the board
RX3°: CON36.2; also elsewhere on the board
S0_CS: C101.2, R44.1; also elsewhere on the board
S0°: CON21.3; also elsewhere on the board
S1_CS: C107.2, R49.1; also elsewhere on the board
S1°: CON24.3; also elsewhere on the board
S2_CS: C113.2, R56.1; also elsewhere on the board
S2°: CON29.3; also elsewhere on the board
S3_CS: C116.2, R64.1; also elsewhere on the board
S3°: CON34.3; also elsewhere on the board
S4_CS: C123.2, R69.1; also elsewhere on the board
S4°: CON38.3; also elsewhere on the board
S5_CS: C130.2, R77.1; also elsewhere on the board
S5°: CON43.3; also elsewhere on the board
S6_CS: C133.2, R82.1; also elsewhere on the board
S6°: CON47.3; also elsewhere on the board
S7_CS: C136.2, R87.1; also elsewhere on the board
S7°: CON51.3; also elsewhere on the board
SCL0°: CON49.4; also elsewhere on the board
SCL1°: CON53.4; also elsewhere on the board
SCLK0°: CON40.2; also elsewhere on the board
SCLK1°: CON45.2; also elsewhere on the board
SDA0°: CON49.2; also elsewhere on the board
SDA1°: CON53.2; also elsewhere on the board
SS0°: CON40.3; also elsewhere on the board
SS1°: CON45.3; also elsewhere on the board
TELEM°: CON31.5; also elsewhere on the board
TX0°: CON18.3; also elsewhere on the board
TX1°: CON26.3; also elsewhere on the board
TX2°: CON31.3; also elsewhere on the board
TX3°: CON36.3; also elsewhere on the board

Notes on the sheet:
SERVOs
ANALOG I/O
REV 0
AUTHOR : JEREMY S.
DATE : 2016-30-10
DESCRIPTION:
BOARD : EXPANSION BOARD
PROJECT: EUROBOT 2017 - MOON VILLAGE
POWER SECTION AND ANALOG
DIGITAL
UARTs
SPIs
I2Cs
MOTOR QEI

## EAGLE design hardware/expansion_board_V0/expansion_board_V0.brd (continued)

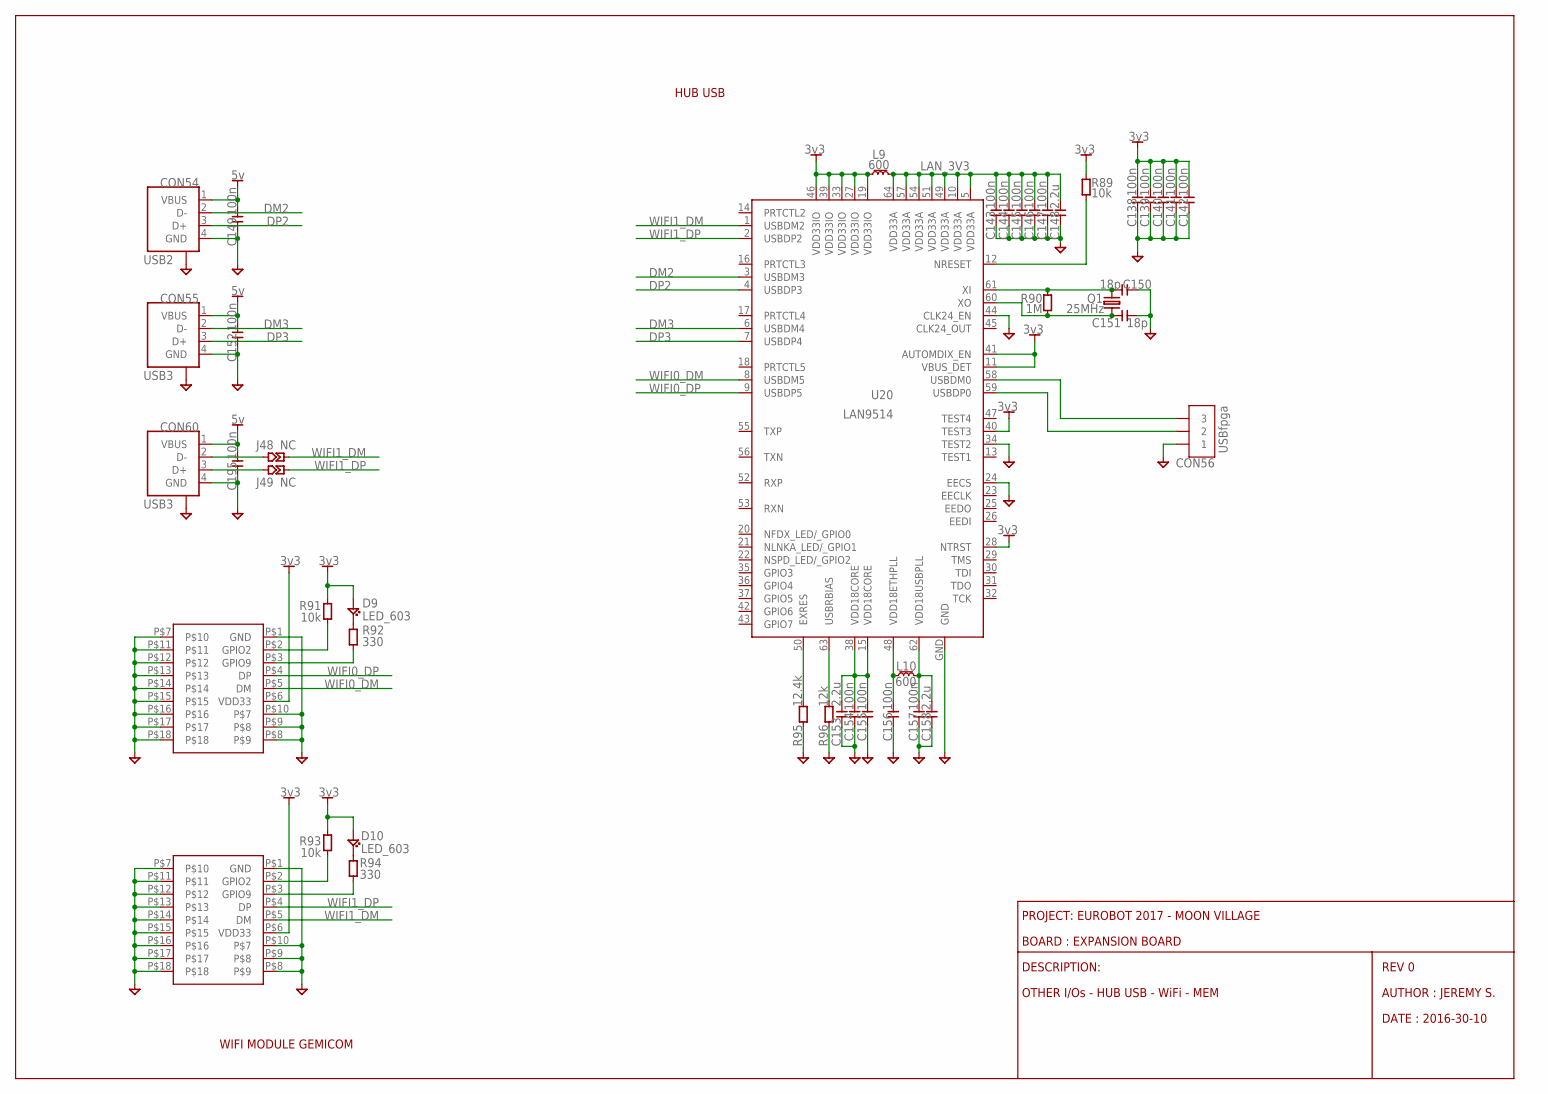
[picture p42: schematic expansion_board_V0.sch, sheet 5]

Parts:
C138, C139, C140, C141, C142, C143, C144, C145, C146, C147, C149, C152, C154, C155, C156, C157, C195: 100n; CAPC1005X55N
C148, C153, C158: 2.2u; CAPC1608X95N
C150, C151: 18p; CAPC1005X55N
CON54: USB2; USB_A
CON55, CON60: USB3; USB_A
CON56: USBfpga; CON254P762X400-3N-S
D9, D10: LED_603; LEDC1608X60N
J48, J49: NC; JUMC1005X50N
L9, L10: 600; INDC1608X95N
Q1: 25MHz; XTAL500X320X130N
R89, R91, R93: 10k; RESC1005X40N
R90: 1M; RESC1005X40N
R92, R94: 330; RESC1005X40N
R95: 12.4k; RESC1005X40N
R96: 12k; RESC1005X40N
U20: LAN9514; QFN50P900X900X100-65N
U21, U22: LGA22U

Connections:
3V3: C138.2, C139.2, C140.2, C141.2, C142.2, D9.A, D10.A, L9.1, R89.2, R91.2, R93.2, U20.11 (VBUS_DET), U20.19 (VDD33IO), U20.27 (VDD33IO), U20.28 (NTRST), U20.33 (VDD33IO), U20.39 (VDD33IO), U20.40 (TEST3), U20.41 (AUTOMDIX_EN), U20.46 (VDD33IO), U21.P$6 (VDD33), U22.P$6 (VDD33); also elsewhere on the board
5V: C149.2, C152.2, C195.2, CON54.1 (VBUS), CON55.1 (VBUS), CON60.1 (VBUS); also elsewhere on the board
DM2: CON54.2 (D-), U20.3 (USBDM3)
DM3: CON55.2 (D-), U20.6 (USBDM4)
DP2: CON54.3 (D+), U20.4 (USBDP3)
DP3: CON55.3 (D+), U20.7 (USBDP4)
GND: C138.1, C139.1, C140.1, C141.1, C142.1, C143.1, C144.1, C145.1, C146.1, C147.1, C148.P$1, C149.1, C150.1, C151.1, C152.1, C153.P$1, C154.1, C155.1, C156.1, C157.1, C158.P$1, C195.1, CON54.4 (GND), CON54.GND1 (GND), CON54.GND2 (GND), CON55.4 (GND), CON55.GND1 (GND), CON55.GND2 (GND), CON56.1, CON60.4 (GND), CON60.GND1 (GND), CON60.GND2 (GND), R95.1, R96.1, U20.24 (EECS), U20.34 (TEST2), U20.44 (CLK24_EN), U20.GND, U21.P$1 (GND), U21.P$7, U21.P$8, U21.P$9, U21.P$10, U21.P$11, U21.P$12, U21.P$13, U21.P$14, U21.P$15, U21.P$16, U21.P$17, U21.P$18, U22.P$1 (GND), U22.P$7, U22.P$8, U22.P$9, U22.P$10, U22.P$11, U22.P$12, U22.P$13, U22.P$14, U22.P$15, U22.P$16, U22.P$17, U22.P$18; also elsewhere on the board
LAN_3V3: C143.2, C144.2, C145.2, C146.2, C147.2, C148.P$2, L9.2, U20.5 (VDD33A), U20.10 (VDD33A), U20.49 (VDD33A), U20.51 (VDD33A), U20.54 (VDD33A), U20.57 (VDD33A), U20.64 (VDD33A)
unnamed: CON60.2 (D-), J48.P$1 (1)
unnamed: CON60.3 (D+), J49.P$1 (1)
unnamed: D10.C, R94.2
unnamed: D9.C, R92.2
unnamed: C157.2, C158.P$2, L10.2, U20.62 (VDD18USBPLL)
unnamed: C153.P$2, C154.2, C155.2, U20.15 (VDD18CORE), U20.38 (VDD18CORE)
unnamed: C156.2, L10.1, U20.48 (VDD18ETHPLL)
unnamed: R95.2, U20.50 (EXRES)
unnamed: R96.2, U20.63 (USBRBIAS)
unnamed: C151.2, Q1.2, R90.1, U20.60 (XO)
unnamed: CON56.2, U20.59 (USBDP0)
unnamed: CON56.3, U20.58 (USBDM0)
unnamed: R89.1, U20.12 (NRESET)
unnamed: C150.2, Q1.1, R90.2, U20.61 (XI)
WIFI0_DM: U20.8 (USBDM5), U21.P$5 (DM)
WIFI0_DP: U20.9 (USBDP5), U21.P$4 (DP)
WIFI1_DM: J48.P$2 (2), U20.1 (USBDM2), U22.P$5 (DM)
WIFI1_DP: J49.P$2 (2), U20.2 (USBDP2), U22.P$4 (DP)
WIFI1_LED: R94.1, U22.P$3 (GPIO9)
WIFI1_LED1: R92.1, U21.P$3 (GPIO9)
WIFI1_WPS: R93.1, U22.P$2 (GPIO2)
WIFI1_WPS1: R91.1, U21.P$2 (GPIO2)

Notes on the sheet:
REV 0
AUTHOR : JEREMY S.
DATE : 2016-30-10
DESCRIPTION:
BOARD : EXPANSION BOARD
PROJECT: EUROBOT 2017 - MOON VILLAGE
OTHER I/Os - HUB USB - WiFi - MEM
HUB USB
WIFI MODULE GEMICOM

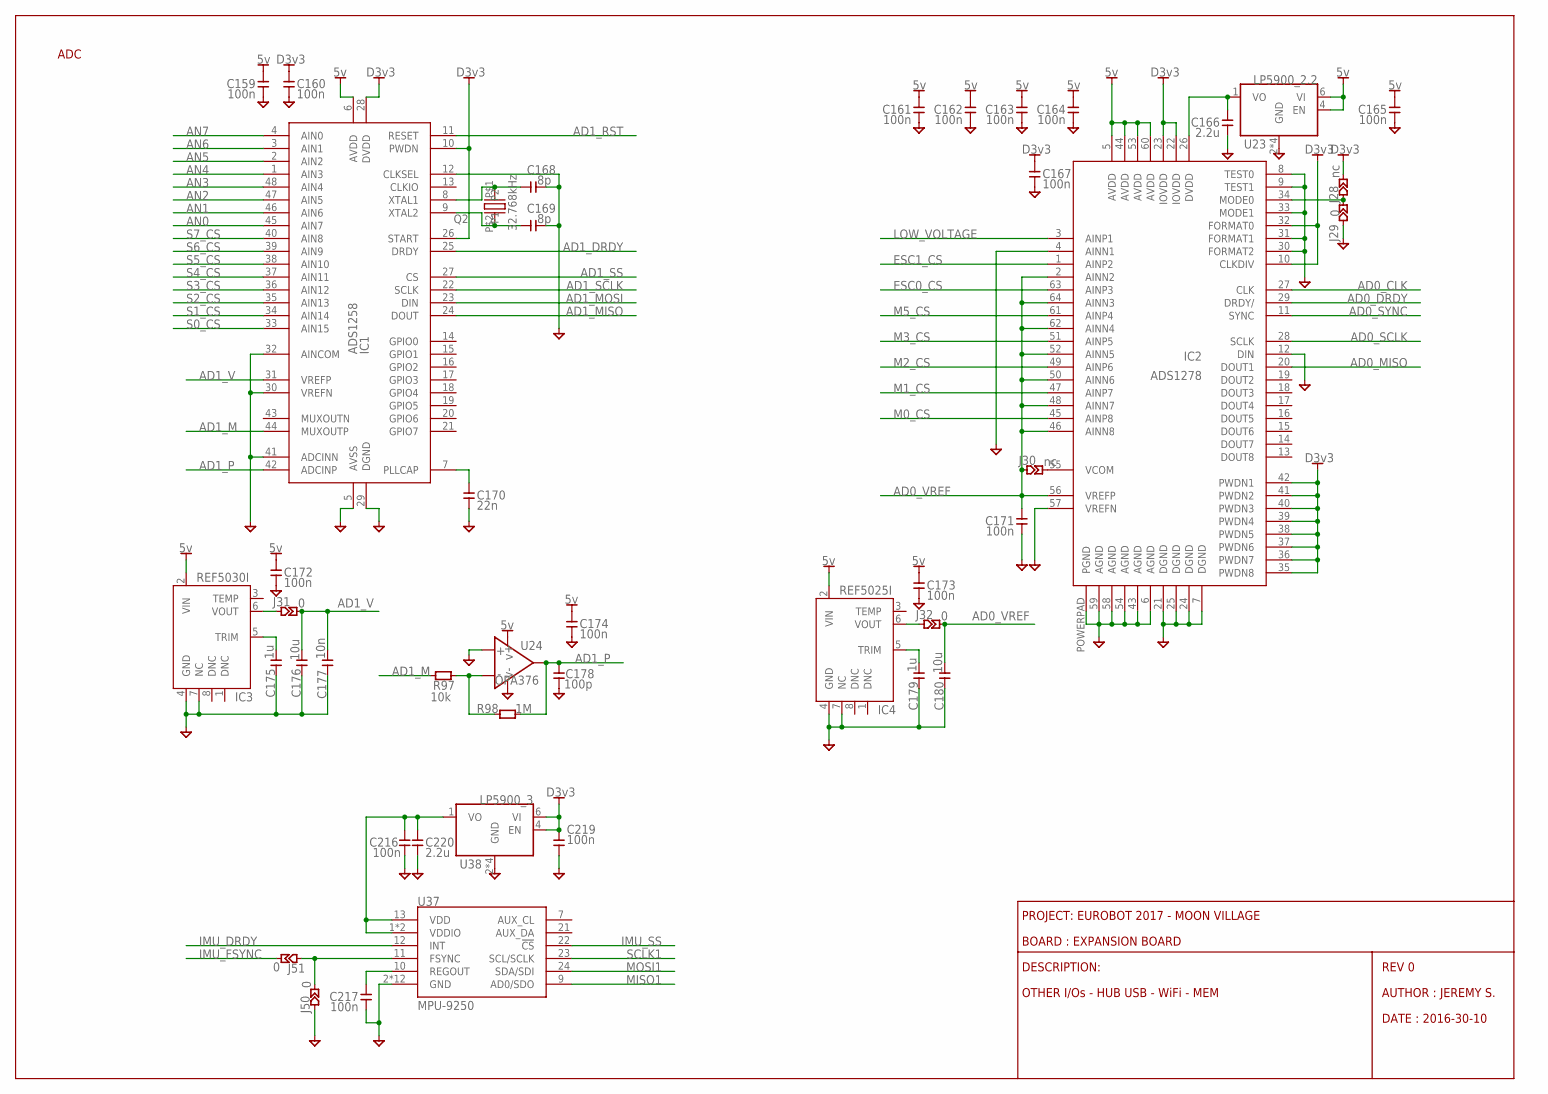
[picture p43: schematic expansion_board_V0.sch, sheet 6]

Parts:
C159, C160, C161, C162, C163, C164, C165, C167, C171, C172, C173, C174, C216, C217, C219: 100n; CAPC1005X55N
C166, C220: 2.2u; CAPC1608X95N
C168, C169: 8p; CAPC1005X55N
C170: 22n; CAPC1005X55N
C175, C179: 1u; CAPC1608X95N
C176, C180: 10u; CAPC2013X100N
C177: 10n; CAPC1005X55N
C178: 100p; CAPC1005X55N
IC1: ADS1258; QFN48
IC2: ADS1278; TQFP64_POWERPAD
IC3: REF5030I; MSOP8_0.65
IC4: REF5025I; MSOP8_0.65
J28, J30: nc; JUMC1005X50N
J29, J31, J32, J50, J51: 0; JUMC1005X50N
Q2: 32.768kHz; 1206
R97: 10k; RESC1005X40N
R98: 1M; RESC1005X40N
U23: LP5900_2.2; SON65P250X220X80-7N
U24: OPA376; SC70-5N
U37: MPU-9250; QFN24-3X3
U38: LP5900_3; SON65P250X220X80-7N

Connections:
5V: C159.2, C161.2, C162.2, C163.2, C164.2, C165.2, C172.2, C173.2, C174.2, IC1.6 (AVDD), IC2.5 (AVDD), IC2.44 (AVDD), IC2.53 (AVDD), IC2.60 (AVDD), IC3.2 (VIN), IC4.2 (VIN), U23.4 (EN), U23.6 (VI), U24.P$5 (VCC); also elsewhere on the board
AD0_CLK: IC2.27 (CLK); also elsewhere on the board
AD0_DRDY: IC2.29 (DRDY/); also elsewhere on the board
AD0_MISO: IC2.20 (DOUT1); also elsewhere on the board
AD0_SCLK: IC2.28 (SCLK); also elsewhere on the board
AD0_SYNC: IC2.11 (SYNC); also elsewhere on the board
AD0_VREF: C171.2, C180.P$1, IC2.2 (AINN2), IC2.46 (AINN8), IC2.48 (AINN7), IC2.50 (AINN6), IC2.52 (AINN5), IC2.56 (VREFP), IC2.62 (AINN4), IC2.64 (AINN3), J30.P$1 (1), J32.P$2 (2); also elsewhere on the board
AD1_DRDY: IC1.25 (DRDY); also elsewhere on the board
AD1_M: IC1.44 (MUXOUTP), R97.1
AD1_MISO: IC1.24 (DOUT); also elsewhere on the board
AD1_MOSI: IC1.23 (DIN); also elsewhere on the board
AD1_P: C178.2, IC1.42 (ADCINP), R98.2, U24.P$4 (OUT)
AD1_RST: IC1.11 (RESET); also elsewhere on the board
AD1_SCLK: IC1.22 (SCLK); also elsewhere on the board
AD1_SS: IC1.27 (CS); also elsewhere on the board
AD1_V: C176.P$1, C177.2, IC1.31 (VREFP), J31.P$2 (2)
AN0: IC1.45 (AIN7); also elsewhere on the board
AN1: IC1.46 (AIN6); also elsewhere on the board
AN2: IC1.47 (AIN5); also elsewhere on the board
AN3: IC1.48 (AIN4); also elsewhere on the board
AN4: IC1.1 (AIN3); also elsewhere on the board
AN5: IC1.2 (AIN2); also elsewhere on the board
AN6: IC1.3 (AIN1); also elsewhere on the board
AN7: IC1.4 (AIN0); also elsewhere on the board
D3V3: C160.2, C167.2, C219.2, IC1.10 (PWDN), IC1.26 (START), IC1.28 (DVDD), IC2.10 (CLKDIV), IC2.22 (IOVDD), IC2.23 (IOVDD), IC2.32 (FORMAT0), IC2.35 (PWDN8), IC2.36 (PWDN7), IC2.37 (PWDN6), IC2.38 (PWDN5), IC2.39 (PWDN4), IC2.40 (PWDN3), IC2.41 (PWDN2), IC2.42 (PWDN1), J28.P$2 (2), U38.4 (EN), U38.6 (VI); also elsewhere on the board
ESC0_CS: IC2.63 (AINP3); also elsewhere on the board
ESC1_CS: IC2.1 (AINP2); also elsewhere on the board
GND: C159.1, C160.1, C161.1, C162.1, C163.1, C164.1, C165.1, C166.P$1, C167.1, C168.1, C169.1, C170.1, C171.1, C172.1, C173.1, C174.1, C175.P$2, C176.P$2, C177.1, C178.1, C179.P$2, C180.P$2, C216.1, C217.1, C219.1, C220.P$1, IC1.5 (AVSS), IC1.12 (CLKSEL), IC1.29 (DGND), IC1.30 (VREFN), IC1.32 (AINCOM), IC1.41 (ADCINN), IC2.4 (AINN1), IC2.6 (AGND), IC2.7 (DGND), IC2.8 (TEST0), IC2.9 (TEST1), IC2.12 (DIN), IC2.21 (DGND), IC2.24 (DGND), IC2.25 (DGND), IC2.30 (FORMAT2), IC2.31 (FORMAT1), IC2.33 (MODE1), IC2.43 (AGND), IC2.54 (AGND), IC2.57 (VREFN), IC2.58 (AGND), IC2.59 (AGND), IC2.POWERPAD (PGND), IC3.4 (GND), IC3.7 (NC), IC4.4 (GND), IC4.7 (NC), J29.P$1 (1), J50.P$1 (1), U23.2 (GND), U23.3 (GND), U23.5 (GND), U23.GND, U24.P$1 (+), U24.P$2 (GND), U37.2 (GND), U37.3 (GND), U37.4 (GND), U37.5 (GND), U37.6 (GND), U37.14 (GND), U37.15 (GND), U37.16 (GND), U37.17 (GND), U37.18 (GND), U37.20 (GND), U37.PAD (GND), U38.2 (GND), U38.3 (GND), U38.5 (GND), U38.GND; also elsewhere on the board
IMU_DRDY: U37.12 (INT); also elsewhere on the board
IMU_FSYNC: J51.P$2 (2); also elsewhere on the board
IMU_SS: U37.22 (!CS); also elsewhere on the board
LOW_VOLTAGE: IC2.3 (AINP1); also elsewhere on the board
M0_CS: IC2.45 (AINP8); also elsewhere on the board
M1_CS: IC2.47 (AINP7); also elsewhere on the board
M2_CS: IC2.49 (AINP6); also elsewhere on the board
M3_CS: IC2.51 (AINP5); also elsewhere on the board
M5_CS: IC2.61 (AINP4); also elsewhere on the board
MISO1: U37.9 (AD0/SDO); also elsewhere on the board
MOSI1: U37.24 (SDA/SDI); also elsewhere on the board
unnamed: R97.2, R98.1, U24.P$3 (-)
unnamed: C168.2, IC1.8 (XTAL1), Q2.P$1 (P1)
unnamed: C175.P$1, IC3.5 (TRIM)
unnamed: IC3.6 (VOUT), J31.P$1 (1)
unnamed: C170.2, IC1.7 (PLLCAP)
unnamed: C169.2, IC1.9 (XTAL2), Q2.P$2 (P2)
unnamed: C216.2, C220.P$2, U37.1 (VDDIO), U37.8 (VDDIO), U37.13 (VDD), U38.1 (VO)
unnamed: J50.P$2 (2), J51.P$1 (1), U37.11 (FSYNC)
unnamed: IC2.55 (VCOM), J30.P$2 (2)
unnamed: IC2.34 (MODE0), J28.P$1 (1), J29.P$2 (2)
unnamed: C179.P$1, IC4.5 (TRIM)
unnamed: C166.P$2, IC2.26 (DVDD), U23.1 (VO)
unnamed: IC4.6 (VOUT), J32.P$1 (1)
REGOUT1: C217.2, U37.10 (REGOUT)
S0_CS: IC1.33 (AIN15); also elsewhere on the board
S1_CS: IC1.34 (AIN14); also elsewhere on the board
S2_CS: IC1.35 (AIN13); also elsewhere on the board
S3_CS: IC1.36 (AIN12); also elsewhere on the board
S4_CS: IC1.37 (AIN11); also elsewhere on the board
S5_CS: IC1.38 (AIN10); also elsewhere on the board
S6_CS: IC1.39 (AIN9); also elsewhere on the board
S7_CS: IC1.40 (AIN8); also elsewhere on the board
SCLK1: U37.23 (SCL/SCLK); also elsewhere on the board

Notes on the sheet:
ADC
REV 0
AUTHOR : JEREMY S.
DATE : 2016-30-10
DESCRIPTION:
BOARD : EXPANSION BOARD
PROJECT: EUROBOT 2017 - MOON VILLAGE
OTHER I/Os - HUB USB - WiFi - MEM

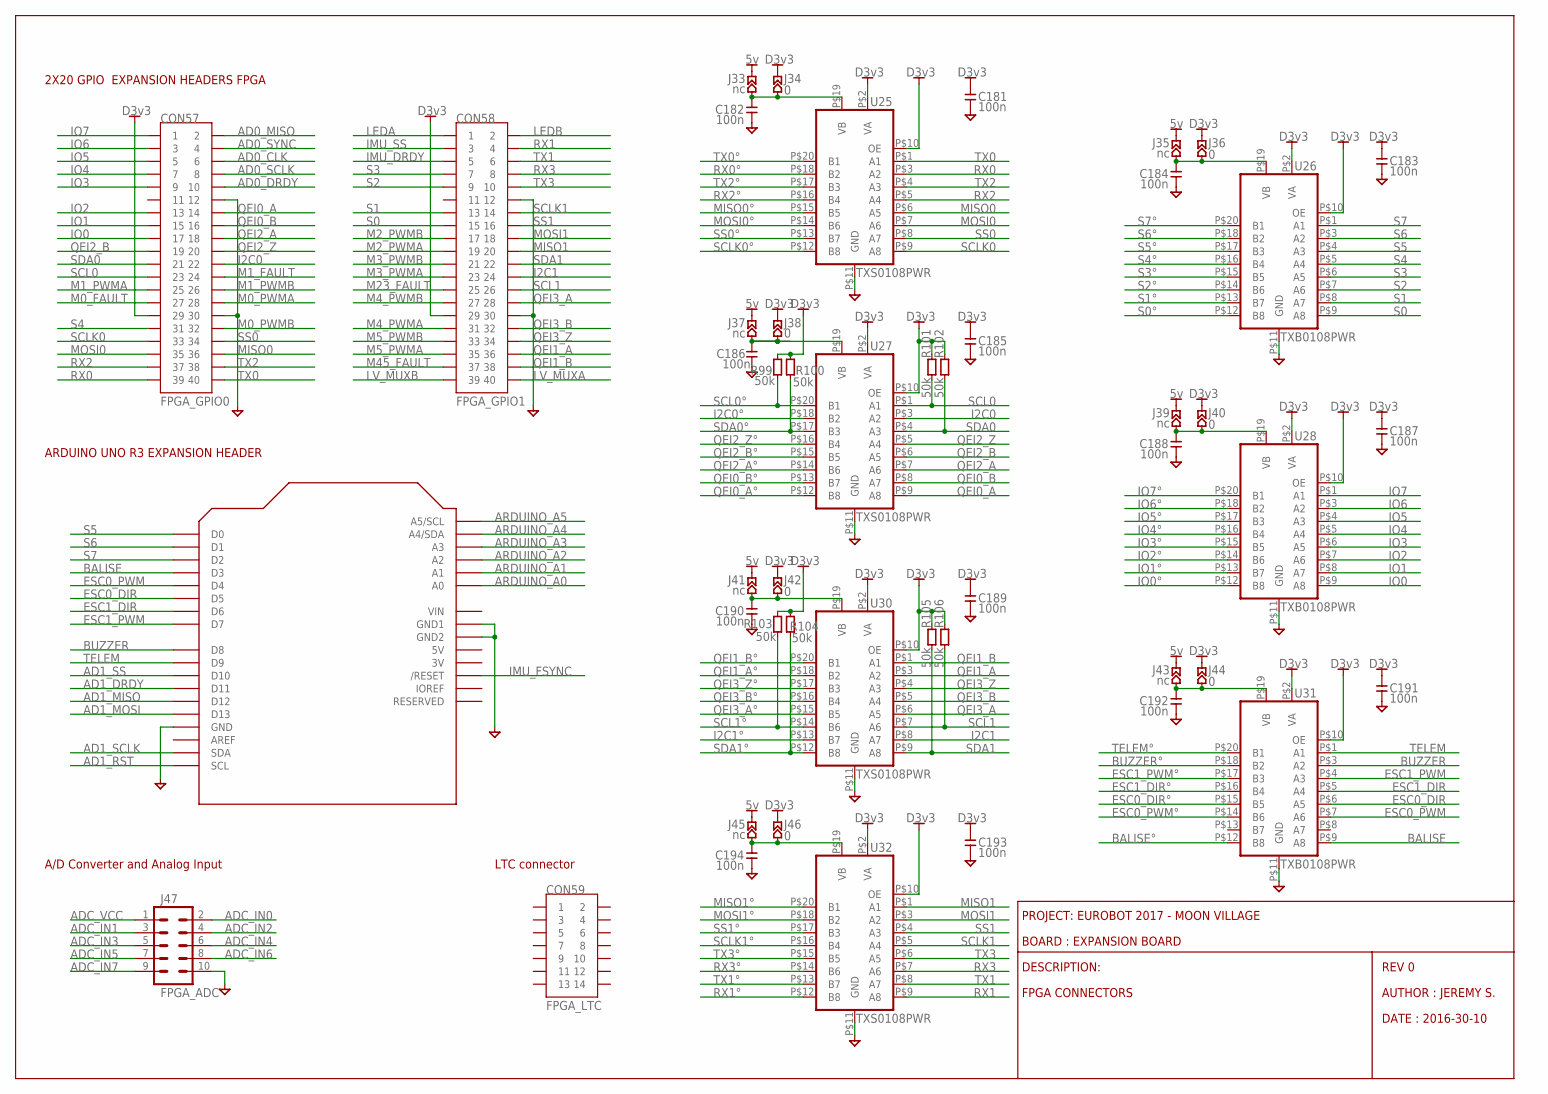
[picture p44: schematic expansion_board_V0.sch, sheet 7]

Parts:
C181, C182, C183, C184, C185, C186, C187, C188, C189, C190, C191, C192, C193, C194: 100n; CAPC1005X55N
CON57: FPGA_GPIO0; CON254P5080X600-40N
CON58: FPGA_GPIO1; CON254P5080X600-40N
CON59: FPGA_LTC; CON200P1700X400-2X7N
J33, J35, J37, J39, J41, J43, J45: nc; JUMC1005X50N
J34, J36, J38, J40, J42, J44, J46: 0; JUMC1005X50N
J47: FPGA_ADC; 2X5_NOSILK
R99, R100, R101, R102, R103, R104, R105, R106: 50k; RESC1005X40N
U25, U27, U30, U32: TXS0108PWR; SOP65P640X110-20N
U26, U28, U31: TXB0108PWR; SOP65P640X110-20N
U29: FPGA_ARDUINO; ARDUINOR3

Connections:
5V: J33.P$2 (2), J35.P$2 (2), J37.P$2 (2), J39.P$2 (2), J41.P$2 (2), J43.P$2 (2), J45.P$2 (2); also elsewhere on the board
AD0_CLK: CON57.6; also elsewhere on the board
AD0_DRDY: CON57.10; also elsewhere on the board
AD0_MISO: CON57.2; also elsewhere on the board
AD0_SCLK: CON57.8; also elsewhere on the board
AD0_SYNC: CON57.4; also elsewhere on the board
AD1_DRDY: U29.D11; also elsewhere on the board
AD1_MISO: U29.D12; also elsewhere on the board
AD1_MOSI: U29.D13; also elsewhere on the board
AD1_RST: U29.SCL; also elsewhere on the board
AD1_SCLK: U29.SDA; also elsewhere on the board
AD1_SS: U29.D10; also elsewhere on the board
ADC_IN0: J47.2
ADC_IN1: J47.3
ADC_IN2: J47.4
ADC_IN3: J47.5
ADC_IN4: J47.6
ADC_IN5: J47.7
ADC_IN6: J47.8
ADC_IN7: J47.9
ADC_VCC: J47.1
ARDUINO_A0: U29.A0
ARDUINO_A1: U29.A1
ARDUINO_A2: U29.A2
ARDUINO_A3: U29.A3
ARDUINO_A4: U29.A4 (A4/SDA)
ARDUINO_A5: U29.A5 (A5/SCL)
BALISE: U29.D3, U31.P$9 (A8)
BALISE°: U31.P$12 (B8); also elsewhere on the board
BUZZER: U29.D8, U31.P$3 (A2)
BUZZER°: U31.P$18 (B2); also elsewhere on the board
D3V3: C181.2, C183.2, C185.2, C187.2, C189.2, C191.2, C193.2, CON57.29, CON58.29, J34.P$2 (2), J36.P$2 (2), J38.P$2 (2), J40.P$2 (2), J42.P$2 (2), J44.P$2 (2), J46.P$2 (2), R99.2, R100.2, R101.2, R102.2, R103.2, R104.2, R105.2, R106.2, U25.P$2 (VA), U25.P$10 (OE), U26.P$2 (VA), U26.P$10 (OE), U27.P$2 (VA), U27.P$10 (OE), U28.P$2 (VA), U28.P$10 (OE), U30.P$2 (VA), U30.P$10 (OE), U31.P$2 (VA), U31.P$10 (OE), U32.P$2 (VA), U32.P$10 (OE); also elsewhere on the board
ESC0_DIR: U29.D5, U31.P$6 (A5)
ESC0_DIR°: U31.P$15 (B5); also elsewhere on the board
ESC0_PWM: U29.D4, U31.P$7 (A6)
ESC0_PWM°: U31.P$14 (B6); also elsewhere on the board
ESC1_DIR: U29.D6, U31.P$5 (A4)
ESC1_DIR°: U31.P$16 (B4); also elsewhere on the board
ESC1_PWM: U29.D7, U31.P$4 (A3)
ESC1_PWM°: U31.P$17 (B3); also elsewhere on the board
GND: C181.1, C182.1, C183.1, C184.1, C185.1, C186.1, C187.1, C188.1, C189.1, C190.1, C191.1, C192.1, C193.1, C194.1, CON57.12, CON57.30, CON58.12, CON58.30, J47.10, U25.P$11 (GND), U26.P$11 (GND), U27.P$11 (GND), U28.P$11 (GND), U29.GND, U29.GND1, U29.GND2, U30.P$11 (GND), U31.P$11 (GND), U32.P$11 (GND); also elsewhere on the board
I2C0: CON57.22, U27.P$3 (A2)
I2C0°: U27.P$18 (B2); also elsewhere on the board
I2C1: CON58.24, U30.P$8 (A7)
I2C1°: U30.P$13 (B7); also elsewhere on the board
IMU_DRDY: CON58.5; also elsewhere on the board
IMU_FSYNC: U29.RESET (/RESET); also elsewhere on the board
IMU_SS: CON58.3; also elsewhere on the board
IO0: CON57.17, U28.P$9 (A8)
IO0°: U28.P$12 (B8); also elsewhere on the board
IO1: CON57.15, U28.P$8 (A7)
IO1°: U28.P$13 (B7); also elsewhere on the board
IO2: CON57.13, U28.P$7 (A6)
IO2°: U28.P$14 (B6); also elsewhere on the board
IO3: CON57.9, U28.P$6 (A5)
IO3°: U28.P$15 (B5); also elsewhere on the board
IO4: CON57.7, U28.P$5 (A4)
IO4°: U28.P$16 (B4); also elsewhere on the board
IO5: CON57.5, U28.P$4 (A3)
IO5°: U28.P$17 (B3); also elsewhere on the board
IO6: CON57.3, U28.P$3 (A2)
IO6°: U28.P$18 (B2); also elsewhere on the board
IO7: CON57.1, U28.P$1 (A1)
IO7°: U28.P$20 (B1); also elsewhere on the board
LEDA: CON58.1; also elsewhere on the board
LEDB: CON58.2; also elsewhere on the board
LV_MUXA: CON58.40; also elsewhere on the board
LV_MUXB: CON58.39; also elsewhere on the board
M0_FAULT: CON57.27; also elsewhere on the board
M0_PWMA: CON57.28; also elsewhere on the board
M0_PWMB: CON57.32; also elsewhere on the board
M1_FAULT: CON57.24; also elsewhere on the board
M1_PWMA: CON57.25; also elsewhere on the board
M1_PWMB: CON57.26; also elsewhere on the board
M2_PWMA: CON58.19; also elsewhere on the board
M2_PWMB: CON58.17; also elsewhere on the board
M3_PWMA: CON58.23; also elsewhere on the board
M3_PWMB: CON58.21; also elsewhere on the board
M4_PWMA: CON58.31; also elsewhere on the board
M4_PWMB: CON58.27; also elsewhere on the board
M5_PWMA: CON58.35; also elsewhere on the board
M5_PWMB: CON58.33; also elsewhere on the board
M23_FAULT: CON58.25; also elsewhere on the board
M45_FAULT: CON58.37; also elsewhere on the board
MISO0: CON57.36, U25.P$6 (A5)
MISO0°: U25.P$15 (B5); also elsewhere on the board
MISO1: CON58.20, U32.P$1 (A1); also elsewhere on the board
MISO1°: U32.P$20 (B1); also elsewhere on the board
MOSI0: CON57.35, U25.P$7 (A6)
MOSI0°: U25.P$14 (B6); also elsewhere on the board
MOSI1: CON58.18, U32.P$3 (A2); also elsewhere on the board
MOSI1°: U32.P$18 (B2); also elsewhere on the board
unnamed: C182.2, J33.P$1 (1), J34.P$1 (1), U25.P$19 (VB)
unnamed: C186.2, J37.P$1 (1), J38.P$1 (1), U27.P$19 (VB)
unnamed: C190.2, J41.P$1 (1), J42.P$1 (1), U30.P$19 (VB)
unnamed: C194.2, J45.P$1 (1), J46.P$1 (1), U32.P$19 (VB)
unnamed: C184.2, J35.P$1 (1), J36.P$1 (1), U26.P$19 (VB)
unnamed: C188.2, J39.P$1 (1), J40.P$1 (1), U28.P$19 (VB)
unnamed: C192.2, J43.P$1 (1), J44.P$1 (1), U31.P$19 (VB)
QEI0_A: CON57.14, U27.P$9 (A8)
QEI0_A°: U27.P$12 (B8); also elsewhere on the board
QEI0_B: CON57.16, U27.P$8 (A7)
QEI0_B°: U27.P$13 (B7); also elsewhere on the board
QEI1_A: CON58.36, U30.P$3 (A2)
QEI1_A°: U30.P$18 (B2); also elsewhere on the board
QEI1_B: CON58.38, U30.P$1 (A1)
QEI1_B°: U30.P$20 (B1); also elsewhere on the board
QEI2_A: CON57.18, U27.P$7 (A6)
QEI2_A°: U27.P$14 (B6); also elsewhere on the board
QEI2_B: CON57.19, U27.P$6 (A5)
QEI2_B°: U27.P$15 (B5); also elsewhere on the board
QEI2_Z: CON57.20, U27.P$5 (A4)
QEI2_Z°: U27.P$16 (B4); also elsewhere on the board
QEI3_A: CON58.28, U30.P$6 (A5)
QEI3_A°: U30.P$15 (B5); also elsewhere on the board
QEI3_B: CON58.32, U30.P$5 (A4)
QEI3_B°: U30.P$16 (B4); also elsewhere on the board
QEI3_Z: CON58.34, U30.P$4 (A3)
QEI3_Z°: U30.P$17 (B3); also elsewhere on the board
RX0: CON57.39, U25.P$3 (A2)
RX0°: U25.P$18 (B2); also elsewhere on the board
RX1: CON58.4, U32.P$9 (A8)
RX1°: U32.P$12 (B8); also elsewhere on the board
RX2: CON57.37, U25.P$5 (A4)
RX2°: U25.P$16 (B4); also elsewhere on the board
RX3: CON58.8, U32.P$7 (A6)
RX3°: U32.P$14 (B6); also elsewhere on the board
S0: CON58.15, U26.P$9 (A8)
S0°: U26.P$12 (B8); also elsewhere on the board
S1: CON58.13, U26.P$8 (A7)
S1°: U26.P$13 (B7); also elsewhere on the board
S2: CON58.9, U26.P$7 (A6)
S2°: U26.P$14 (B6); also elsewhere on the board
S3: CON58.7, U26.P$6 (A5)
S3°: U26.P$15 (B5); also elsewhere on the board
S4: CON57.31, U26.P$5 (A4)
S4°: U26.P$16 (B4); also elsewhere on the board
S5: U26.P$4 (A3), U29.D0
S5°: U26.P$17 (B3); also elsewhere on the board
S6: U26.P$3 (A2), U29.D1
S6°: U26.P$18 (B2); also elsewhere on the board
S7: U26.P$1 (A1), U29.D2
S7°: U26.P$20 (B1); also elsewhere on the board
SCL0: CON57.23, R101.1, U27.P$1 (A1)
SCL0°: R99.1, U27.P$20 (B1); also elsewhere on the board
SCL1: CON58.26, R106.1, U30.P$7 (A6)
SCL1°: R103.1, U30.P$14 (B6); also elsewhere on the board
SCLK0: CON57.33, U25.P$9 (A8)
SCLK0°: U25.P$12 (B8); also elsewhere on the board
SCLK1: CON58.14, U32.P$5 (A4); also elsewhere on the board
SCLK1°: U32.P$16 (B4); also elsewhere on the board
SDA0: CON57.21, R102.1, U27.P$4 (A3)
SDA0°: R100.1, U27.P$17 (B3); also elsewhere on the board
SDA1: CON58.22, R105.1, U30.P$9 (A8)
SDA1°: R104.1, U30.P$12 (B8); also elsewhere on the board
SS0: CON57.34, U25.P$8 (A7)
SS0°: U25.P$13 (B7); also elsewhere on the board
SS1: CON58.16, U32.P$4 (A3)
SS1°: U32.P$17 (B3); also elsewhere on the board
TELEM: U29.D9, U31.P$1 (A1)
TELEM°: U31.P$20 (B1); also elsewhere on the board
TX0: CON57.40, U25.P$1 (A1)
TX0°: U25.P$20 (B1); also elsewhere on the board
TX1: CON58.6, U32.P$8 (A7)
TX1°: U32.P$13 (B7); also elsewhere on the board
TX2: CON57.38, U25.P$4 (A3)
TX2°: U25.P$17 (B3); also elsewhere on the board
TX3: CON58.10, U32.P$6 (A5)
TX3°: U32.P$15 (B5); also elsewhere on the board

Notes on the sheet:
REV 0
AUTHOR : JEREMY S.
DATE : 2016-30-10
DESCRIPTION:
BOARD : EXPANSION BOARD
PROJECT: EUROBOT 2017 - MOON VILLAGE
FPGA CONNECTORS
2X20 GPIO EXPANSION HEADERS FPGA
ARDUINO UNO R3 EXPANSION HEADER
A/D Converter and Analog Input
LTC connector

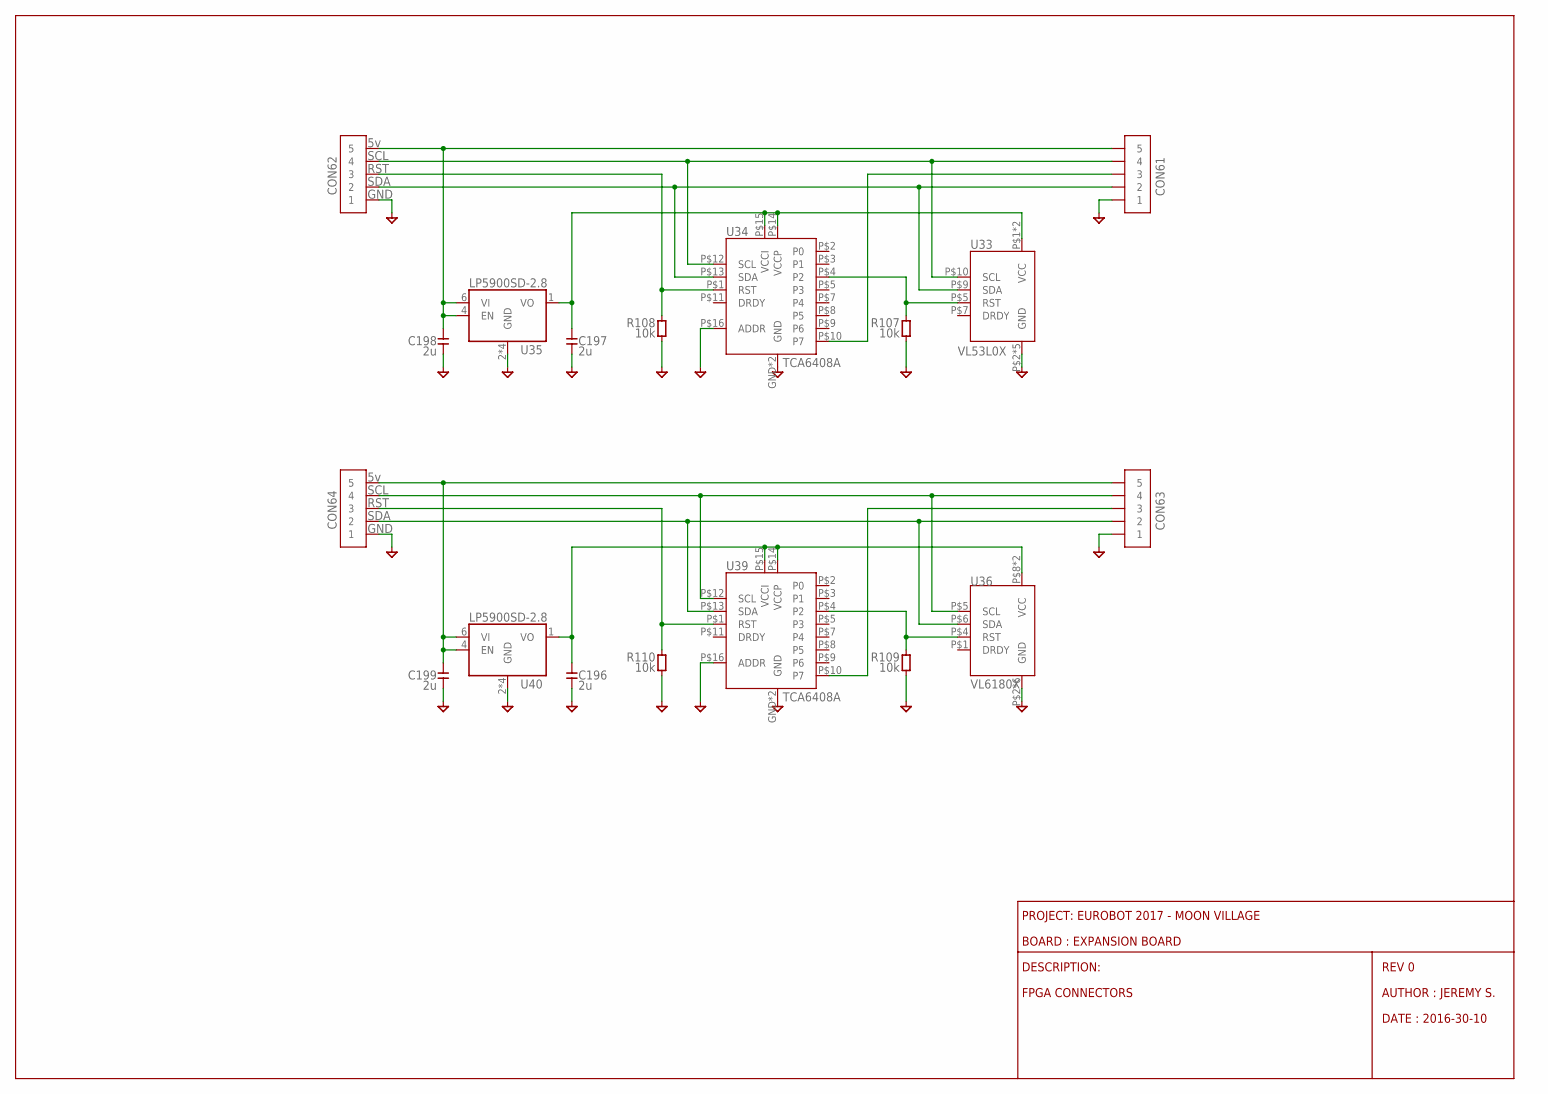
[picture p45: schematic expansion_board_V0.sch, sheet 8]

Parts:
C196, C197, C198, C199: 2u; CAPC1608X95N
CON61, CON62, CON63, CON64: CON5_2.54S; CON254P1270X400-5S
R107, R108, R109, R110: 10k; RESC1005X40N
U33: VL53L0X
U34, U39: TCA6408A; QFN50P300X300X80-17N
U35, U40: LP5900SD-2.8; SON65P250X220X80-7N
U36: VL6180X

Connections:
GND: C196.P$2, C197.P$2, C198.P$2, C199.P$2, CON61.1, CON62.1, CON63.1, CON64.1, R107.2, R108.2, R109.2, R110.2, U33.P$2 (GND), U33.P$3 (GND), U33.P$4 (GND), U33.P$6 (GND), U33.P$12 (GND), U34.GND, U34.P$6 (GND), U34.P$16 (ADDR), U35.2 (GND), U35.3 (GND), U35.5 (GND), U35.GND, U36.P$2 (GND), U36.P$3 (GND), U36.P$7 (GND), U36.P$9 (GND), U36.P$11 (GND), U36.P$12 (GND), U39.GND, U39.P$6 (GND), U39.P$16 (ADDR), U40.2 (GND), U40.3 (GND), U40.5 (GND), U40.GND; also elsewhere on the board
unnamed: R107.1, U33.P$5 (RST), U34.P$4 (P2)
unnamed: CON62.3, R108.1, U34.P$1 (RST)
unnamed: CON61.2, CON62.2, U33.P$9 (SDA), U34.P$13 (SDA)
unnamed: CON61.4, CON62.4, U33.P$10 (SCL), U34.P$12 (SCL)
unnamed: CON61.3, U34.P$10 (P7)
unnamed: C198.P$1, CON61.5, CON62.5, U35.4 (EN), U35.6 (VI)
unnamed: C197.P$1, U33.P$1 (VCC), U33.P$11 (VCC), U34.P$14 (VCCP), U34.P$15 (VCCI), U35.1 (VO)
unnamed: C199.P$1, CON63.5, CON64.5, U40.4 (EN), U40.6 (VI)
unnamed: CON63.4, CON64.4, U36.P$5 (SCL), U39.P$12 (SCL)
unnamed: CON63.2, CON64.2, U36.P$6 (SDA), U39.P$13 (SDA)
unnamed: C196.P$1, U36.P$8 (VCC), U36.P$10 (VCC), U39.P$14 (VCCP), U39.P$15 (VCCI), U40.1 (VO)
unnamed: CON64.3, R110.1, U39.P$1 (RST)
unnamed: CON63.3, U39.P$10 (P7)
unnamed: R109.1, U36.P$4 (RST), U39.P$4 (P2)

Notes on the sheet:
REV 0
AUTHOR : JEREMY S.
DATE : 2016-30-10
DESCRIPTION:
BOARD : EXPANSION BOARD
PROJECT: EUROBOT 2017 - MOON VILLAGE
FPGA CONNECTORS
SDA
RST
SCL
GND

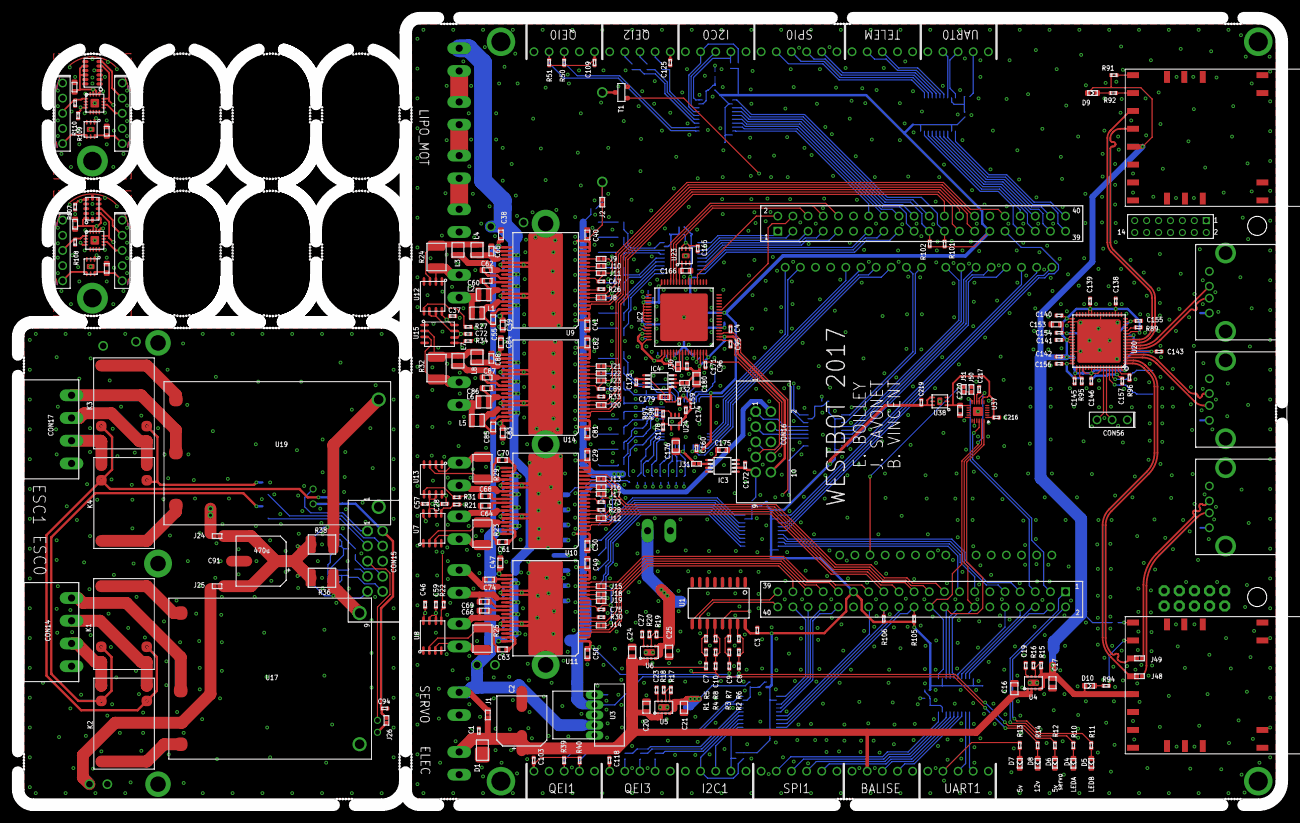
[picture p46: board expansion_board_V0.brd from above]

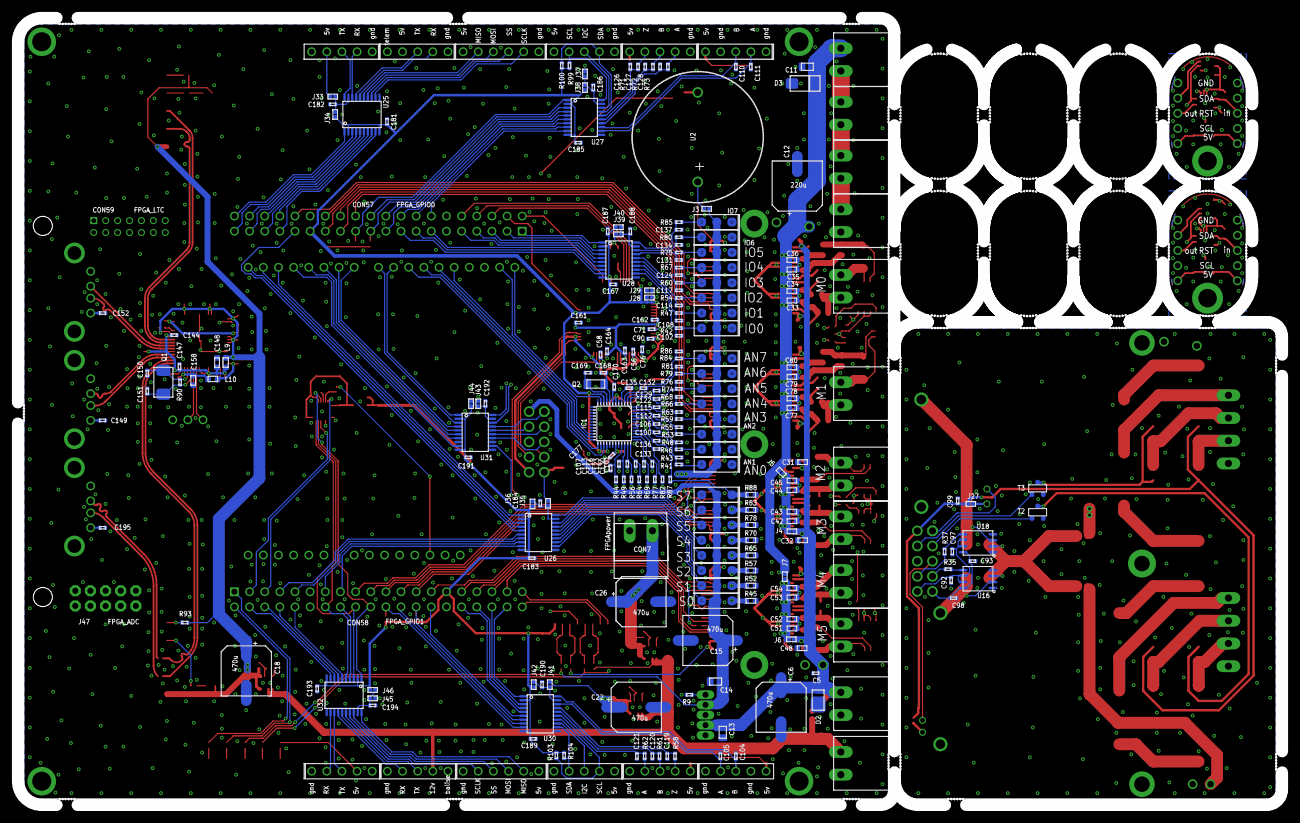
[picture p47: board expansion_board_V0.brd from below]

Board: 4 copper layers, 212.0 x 132.0 mm, 501 parts (250 on the bottom side), 392 nets.

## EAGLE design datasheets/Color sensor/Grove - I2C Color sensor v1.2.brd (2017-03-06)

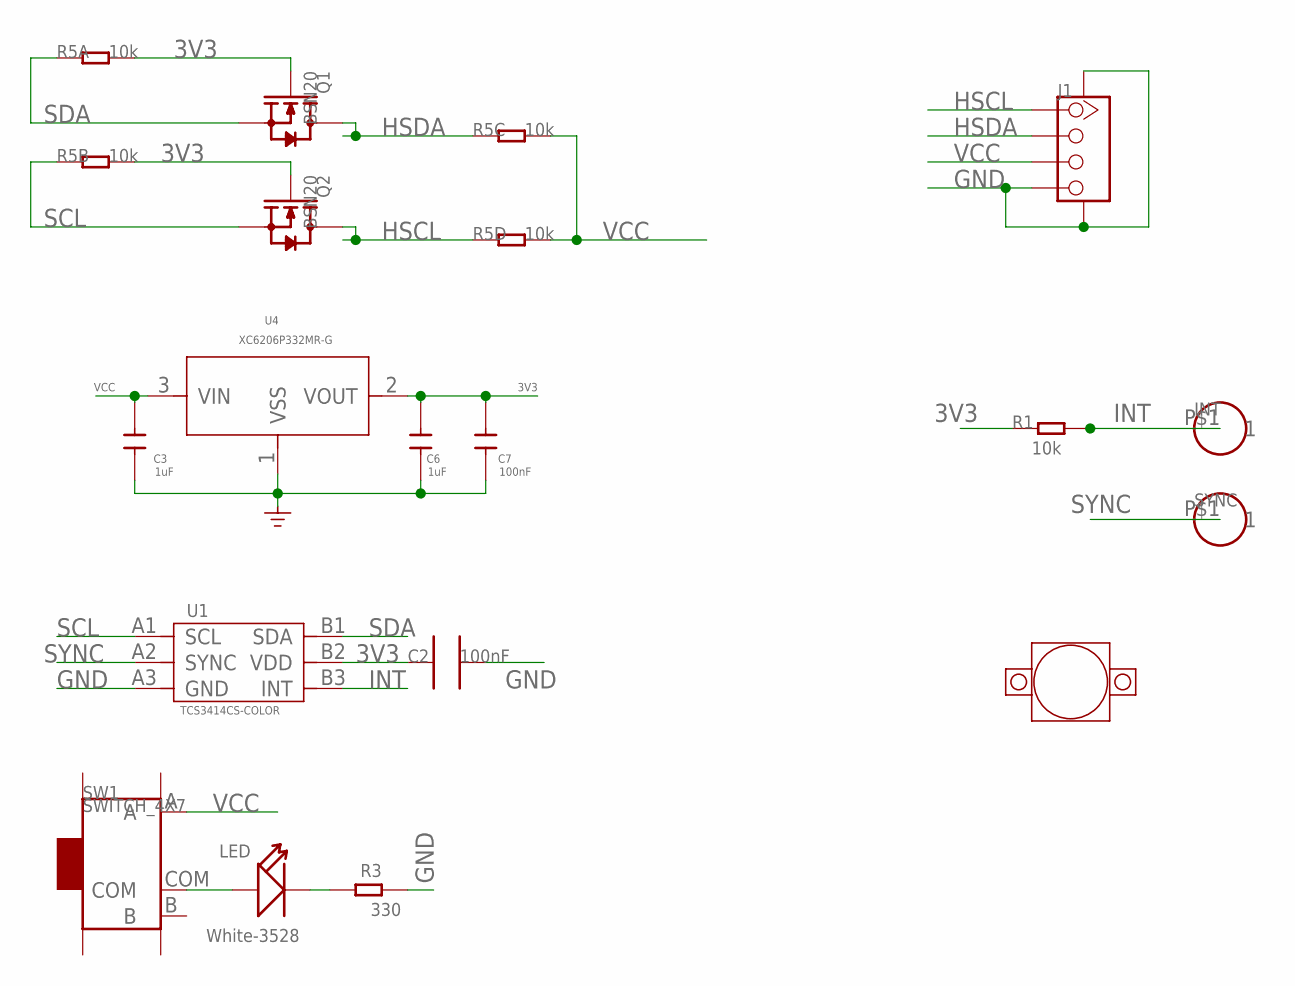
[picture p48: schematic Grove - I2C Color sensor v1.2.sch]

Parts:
C2: 100nF; 0603_S
C3, C6: 1uF; C0603
C7: 100nF; C0603
INT: CK_1X132; CK_1X1
J1: TWIG-4P-2.0-SMD-FEMALE-REINFORCE'DD'; 4P-SMD-2.0
LED: White-3528; LED1210
Q1, Q2: BSN20; SOT23
R1: 10k; 0603
R3: 330; 0603
R5: 10k; R1206-8
SW1: SWITCH_4X7; 4*8_SW
SYNC: CK_1X132; CK_1X1
U1: TCS3414CS-COLOR; TCS3414CS
U3: LENS_HOOD
U4: XC6206P332MR-G; SOT23

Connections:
3V3: C2.1, C6.2, C7.2, Q1.1 (G), Q2.1 (G), R1.1, R5.7 (2), R5.8 (2), U1.B2 (VDD), U4.2 (VOUT)
GND: C2.2, C3.1, C6.1, C7.1, J1.4, J1.SS1, J1.SS2, R3.1, U1.A3 (GND), U4.1 (VSS)
HSCL: J1.1, Q2.3 (D), R5.4 (1)
HSDA: J1.2, Q1.3 (D), R5.3 (1)
INT: INT.P$1, R1.2, U1.B3 (INT)
unnamed: LED.1 (+), SW1.COM
unnamed: LED.2 (-), R3.2
SCL: Q2.2 (S), R5.2 (1), U1.A1 (SCL)
SDA: Q1.2 (S), R5.1, U1.B1 (SDA)
SYNC: SYNC.P$1, U1.A2 (SYNC)
VCC: C3.2, J1.3, R5.5 (2), R5.6 (2), SW1.A, U4.3 (VIN)

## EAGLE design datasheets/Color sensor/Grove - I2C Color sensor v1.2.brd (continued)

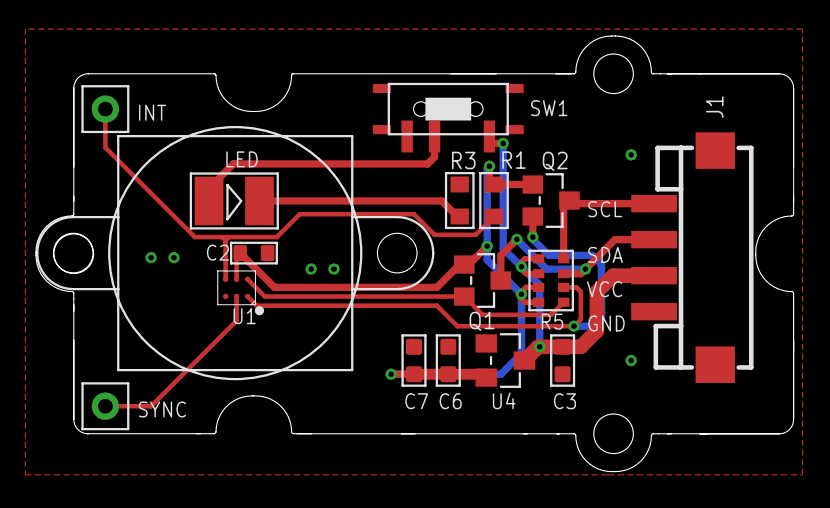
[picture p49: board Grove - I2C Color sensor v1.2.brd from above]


Board: 2 copper layers, 42.1 x 24.2 mm, 20 parts (2 on the bottom side), 11 nets.

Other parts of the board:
U$1: TWIGLOGO
U$2: 2U-DIM-W/-DRILL
U$3: OSHW_FILLX200_NOTEXT

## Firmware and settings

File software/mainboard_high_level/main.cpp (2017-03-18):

// Copyright (c) 2016-2017 All Rights Reserved WestBot

#define SIMU
#define DEBUG

#include <memory>

#include <QCoreApplication>
#ifdef DEBUG
#include <QDebug>
#endif
#include <QThread>

#include "hps_arm.h" // For our base address

#include "GameManager.hpp"
#include "Input.hpp"
#include "ItemRegister.hpp"
#include "Memory.hpp"
#include "MemoryManager.hpp"
#include "Output.hpp"

using namespace WestBot;

QDebug operator<<( QDebug debug, Input::Value value );

int main( int argc, char *argv[] )
{
    QCoreApplication app(argc, argv);

    // Manage the LW_BRIDGE
    MemoryManager memoryManager;

    // Create our layer mapping
    Memory layer1( memoryManager, PIO_N_LAYER1_BASE );
    Memory layer2( memoryManager, PIO_N_LAYER2_BASE );
    Memory layer3( memoryManager, PIO_N_LAYER3_BASE );

#ifdef DEBUG
    // Read layer 1 registers
    qDebug() << "Layer 1 registers:";
    qDebug() << "==================";

    for( int i = 0; i < 64; ++i )
    {
        qDebug()
            << "Read register" << i << ":"
            << QString::number( layer1.read( i * 4, 32 ), 16 );
    }

    // Read layer 2 registers
    qDebug() << "Layer 2 registers:";
    qDebug() << "==================";

    for( int i = 0; i < 64; ++i )
    {
        qDebug()
            << "Read register" << i << ":"
            << QString::number( layer2.read( i * 4, 32 ), 16 );
    }

    // Read layer 3 registers
    qDebug() << "Layer 3 registers:";
    qDebug() << "==================";

    for( int i = 0; i < 64; ++i )
    {
        qDebug()
            << "Read register" << i << ":"
            << QString::number( layer3.read( i * 4, 32 ), 16 );
    }
#endif

#ifdef SIMU
    ItemRegister configStateRegister(
        layer1,
        1 * 4,
        32 );

    configStateRegister.write( 0xffffffff );
#endif

    // INPUT REGISTER
    ItemRegister inputRegister( layer1, 7 * 4, 32 );

    // OUTOUT REGISTER
    ItemRegister outputOverride( layer1, 10 * 4, 32 );
    outputOverride.write( 0x01010101 );

    ItemRegister outputLedRegister( layer1, 9 * 4, 8 );
    ItemRegister outputIO1Register( layer1, 9 * 4 + 1, 8 );
    ItemRegister outputIO2Register( layer1, 9 * 4 + 2, 8 );
    ItemRegister outputIO3Register( layer1, 9 * 4 + 3, 8 );

    // M0
    ItemRegister pwm0Override( layer1, 12 * 4 + 3, 8 );
    pwm0Override.write( 0x01 );

    ItemRegister pwm0( layer1, 12 * 4, 16 );
    pwm0.write( 32000 );

    // Buttons
    Input::Ptr tirette = std::make_shared< Input >( inputRegister, Input::InputType::Start, "Tirette" );
    Input::Ptr color = std::make_shared< Input >( inputRegister, Input::InputType::Color, "Color" );
    Input::Ptr arretUrgence = std::make_shared< Input >( inputRegister, Input::InputType::Stop, "AU" );

    // Leds
    Output led( outputLedRegister, Output::OutputType::Led, "Led" );
    Output io1( outputIO1Register, Output::OutputType::IO1, "IO1" );
    Output io2( outputIO2Register, Output::OutputType::IO2, "IO2" );
    Output io3( outputIO3Register, Output::OutputType::IO3, "IO3" );

    GameManager game( tirette, color, arretUrgence );

    while(1)
    {
        QCoreApplication::processEvents();
    }

    /*
    while( 1 )
    {
        qDebug() << "Tirette:" << tirette->digitalRead();
        qDebug() << "Color:" << color->digitalRead();
        qDebug() << "AU:" << arretUrgence->digitalRead();

        led.digitalWrite( Output::Value::ON );
        io1.digitalWrite( Output::Value::OFF );
        io2.digitalWrite( Output::Value::ON );
        io3.digitalWrite( Output::Value::OFF );
        QThread::msleep( 250 );

        led.digitalWrite( Output::Value::OFF );
        io1.digitalWrite( Output::Value::ON );
        io2.digitalWrite( Output::Value::OFF );
        io3.digitalWrite( Output::Value::ON );
        QThread::msleep( 250 );
    }
    */

    return app.exec();
}

QDebug operator<<( QDebug debug, Input::Value value )
{
    switch( value )
    {
    case Input::Value::OFF:
        debug << "OFF";
        break;

    case Input::Value::ON:
        debug << "ON";
        break;
    }
    return debug;
}

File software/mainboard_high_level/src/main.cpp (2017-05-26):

#include <QObject>
#include <QTimer>
#include <QThread>
#include <QDebug>
#include <QCoreApplication>

#include <WestBot/ExecuteMatch.hpp>

using namespace WestBot;


int main( int argc, char *argv[] )
{
	QCoreApplication app( argc, argv );
	ExecuteMatch match;

	qDebug() << "Thread run";
	match.start();

	while( !match.started ){
		QThread::msleep(100);
		match.displayLed();
	}

	QTimer t;
	t.setSingleShot(true);
	t.start( 90*1000 );

	while( 1 ){
		QThread::msleep(20);

		if( t.remainingTime()<=0 ) {
			qDebug() << "END OF MATCH";
			break;
		}

		if(match.isArretUrgence()) {
			qDebug() << "HARD STOP";
			break;
		}
	}

	match.terminate();
	match.hardStop();

	if(!match.isArretUrgence()) {
		match.funnyAction();
	}


	while(1)
		;

	return 0;
}

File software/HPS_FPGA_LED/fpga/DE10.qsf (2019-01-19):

# -------------------------------------------------------------------------- #
#
# Copyright (C) 1991-2016 Altera Corporation. All rights reserved.
# Your use of Altera Corporation's design tools, logic functions
# and other software and tools, and its AMPP partner logic
# functions, and any output files from any of the foregoing
# (including device programming or simulation files), and any
# associated documentation or information are expressly subject
# to the terms and conditions of the Altera Program License
# Subscription Agreement, the Altera Quartus Prime License Agreement,
# the Altera MegaCore Function License Agreement, or other
# applicable license agreement, including, without limitation,
# that your use is for the sole purpose of programming logic
# devices manufactured by Altera and sold by Altera or its
# authorized distributors.  Please refer to the applicable
# agreement for further details.
#
# -------------------------------------------------------------------------- #
#
# Quartus Prime
# Version 16.0.0 Build 211 04/27/2016 SJ Lite Edition
# Date created = 18:31:04  November 13, 2016
#
# -------------------------------------------------------------------------- #
#
# Notes:
#
# 1) The default values for assignments are stored in the file:
#		DE10_assignment_defaults.qdf
#    If this file doesn't exist, see file:
#		assignment_defaults.qdf
#
# 2) Altera recommends that you do not modify this file. This
#    file is updated automatically by the Quartus Prime software
#    and any changes you make may be lost or overwritten.
#
# -------------------------------------------------------------------------- #


set_global_assignment -name FAMILY "Cyclone V"
set_global_assignment -name DEVICE 5CSEBA6U23I7
set_global_assignment -name TOP_LEVEL_ENTITY HPSFPGA
set_global_assignment -name ORIGINAL_QUARTUS_VERSION 16.1.0
set_global_assignment -name PROJECT_CREATION_TIME_DATE "20:23:32  OCTOBRE 08, 2018"
set_global_assignment -name LAST_QUARTUS_VERSION "16.1.2 Lite Edition"
set_global_assignment -name PROJECT_OUTPUT_DIRECTORY output_files
set_global_assignment -name MIN_CORE_JUNCTION_TEMP "-40"
set_global_assignment -name MAX_CORE_JUNCTION_TEMP 100
set_global_assignment -name ERROR_CHECK_FREQUENCY_DIVISOR 256
set_global_assignment -name EDA_TIME_SCALE "1 ps" -section_id eda_simulation


set_instance_assignment -name IO_STANDARD "3.3-V LVTTL" -to ADC_CONVST
set_instance_assignment -name IO_STANDARD "3.3-V LVTTL" -to ADC_SCK
set_instance_assignment -name IO_STANDARD "3.3-V LVTTL" -to ADC_SDI
set_instance_assignment -name IO_STANDARD "3.3-V LVTTL" -to ADC_SDO
set_instance_assignment -name IO_STANDARD "3.3-V LVTTL" -to s[5]
set_instance_assignment -name IO_STANDARD "3.3-V LVTTL" -to s[6]
set_instance_assignment -name IO_STANDARD "3.3-V LVTTL" -to s[7]
set_instance_assignment -name IO_STANDARD "3.3-V LVTTL" -to uart3_custom
set_instance_assignment -name IO_STANDARD "3.3-V LVTTL" -to esc0_pwm
set_instance_assignment -name IO_STANDARD "3.3-V LVTTL" -to esc0_dir
set_instance_assignment -name IO_STANDARD "3.3-V LVTTL" -to esc1_dir
set_instance_assignment -name IO_STANDARD "3.3-V LVTTL" -to esc1_pwm
set_instance_assignment -name IO_STANDARD "3.3-V LVTTL" -to buzzer
set_instance_assignment -name IO_STANDARD "3.3-V LVTTL" -to uart2_custom
set_instance_assignment -name IO_STANDARD "3.3-V LVTTL" -to ad1_ss
set_instance_assignment -name IO_STANDARD "3.3-V LVTTL" -to ad1_drdy
set_instance_assignment -name IO_STANDARD "3.3-V LVTTL" -to ad1_miso
set_instance_assignment -name IO_STANDARD "3.3-V LVTTL" -to ad1_mosi
set_instance_assignment -name IO_STANDARD "3.3-V LVTTL" -to ad1_sclk
set_instance_assignment -name IO_STANDARD "3.3-V LVTTL" -to ad1_rst
set_instance_assignment -name IO_STANDARD "3.3-V LVTTL" -to imu_fsync
set_instance_assignment -name IO_STANDARD "3.3-V LVTTL" -to FPGA_CLK1_50
set_instance_assignment -name IO_STANDARD "3.3-V LVTTL" -to FPGA_CLK2_50
set_instance_assignment -name IO_STANDARD "3.3-V LVTTL" -to FPGA_CLK3_50
set_instance_assignment -name IO_STANDARD "3.3-V LVTTL" -to io_7
set_instance_assignment -name IO_STANDARD "3.3-V LVTTL" -to ad0_miso
set_instance_assignment -name IO_STANDARD "3.3-V LVTTL" -to io_6
set_instance_assignment -name IO_STANDARD "3.3-V LVTTL" -to ad0_sync
set_instance_assignment -name IO_STANDARD "3.3-V LVTTL" -to io_5
set_instance_assignment -name IO_STANDARD "3.3-V LVTTL" -to ad0_clk
set_instance_assignment -name IO_STANDARD "3.3-V LVTTL" -to io_4
set_instance_assignment -name IO_STANDARD "3.3-V LVTTL" -to ad0_sclk
set_instance_assignment -name IO_STANDARD "3.3-V LVTTL" -to io_3
set_instance_assignment -name IO_STANDARD "3.3-V LVTTL" -to ad0_drdy
set_instance_assignment -name IO_STANDARD "3.3-V LVTTL" -to io_2
set_instance_assignment -name IO_STANDARD "3.3-V LVTTL" -to qei0_a
set_instance_assignment -name IO_STANDARD "3.3-V LVTTL" -to io_1
set_instance_assignment -name IO_STANDARD "3.3-V LVTTL" -to qei0_b
set_instance_assignment -name IO_STANDARD "3.3-V LVTTL" -to io_0
set_instance_assignment -name IO_STANDARD "3.3-V LVTTL" -to qei2_a
set_instance_assignment -name IO_STANDARD "3.3-V LVTTL" -to qei2_b
set_instance_assignment -name IO_STANDARD "3.3-V LVTTL" -to qei2_z
set_instance_assignment -name IO_STANDARD "3.3-V LVTTL" -to i2c0_sda
set_instance_assignment -name IO_STANDARD "3.3-V LVTTL" -to i2c0_reset
set_instance_assignment -name IO_STANDARD "3.3-V LVTTL" -to i2c0_scl
set_instance_assignment -name IO_STANDARD "3.3-V LVTTL" -to m01_resetn
set_instance_assignment -name IO_STANDARD "3.3-V LVTTL" -to m1_pwma
set_instance_assignment -name IO_STANDARD "3.3-V LVTTL" -to m1_pwmb
set_instance_assignment -name IO_STANDARD "3.3-V LVTTL" -to m01_fault
set_instance_assignment -name IO_STANDARD "3.3-V LVTTL" -to m0_pwma
set_instance_assignment -name IO_STANDARD "3.3-V LVTTL" -to s[4]
set_instance_assignment -name IO_STANDARD "3.3-V LVTTL" -to m0_pwmb
set_instance_assignment -name IO_STANDARD "3.3-V LVTTL" -to spi0_sclk
set_instance_assignment -name IO_STANDARD "3.3-V LVTTL" -to spi0_ss
set_instance_assignment -name IO_STANDARD "3.3-V LVTTL" -to spi0_mosi
set_instance_assignment -name IO_STANDARD "3.3-V LVTTL" -to spi0_miso
set_instance_assignment -name IO_STANDARD "3.3-V LVTTL" -to uart2_rx
set_instance_assignment -name IO_STANDARD "3.3-V LVTTL" -to uart2_tx
set_instance_assignment -name IO_STANDARD "3.3-V LVTTL" -to uart0_rx
set_instance_assignment -name IO_STANDARD "3.3-V LVTTL" -to uart0_tx
set_instance_assignment -name IO_STANDARD "3.3-V LVTTL" -to led_green
set_instance_assignment -name IO_STANDARD "3.3-V LVTTL" -to led_red
set_instance_assignment -name IO_STANDARD "3.3-V LVTTL" -to imu_ss
set_instance_assignment -name IO_STANDARD "3.3-V LVTTL" -to uart1_rx
set_instance_assignment -name IO_STANDARD "3.3-V LVTTL" -to imu_drdy
set_instance_assignment -name IO_STANDARD "3.3-V LVTTL" -to uart1_tx
set_instance_assignment -name IO_STANDARD "3.3-V LVTTL" -to s[3]
set_instance_assignment -name IO_STANDARD "3.3-V LVTTL" -to uart3_rx
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

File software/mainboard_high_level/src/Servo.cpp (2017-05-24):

// Copyright (c) 2016-2017 All Rights Reserved WestBot

#include <QDebug>
#include <QThread>
#include <QTime>

#include <WestBot/Servo.hpp>

using namespace WestBot;

Servo::Servo( const QString& name )
    : _name( name )
    , _servo( nullptr )
    , _servoEnable( nullptr )
    , _servoOverride( nullptr )
    , _minAngle( 0 )
    , _maxAngle( 0 )
{
}

bool Servo::attach( Hal& hal,
                    uint8_t ioNumber,
                    uint16_t min,
                    uint16_t max )
{
    switch( ioNumber )
    {
    case 0:
        _servo = std::make_shared< ItemRegister >( hal._s0 );
        _servoEnable = std::make_shared< ItemRegister >( hal._s0Enable );
        _servoOverride = std::make_shared< ItemRegister >( hal._s0Override );
        break;

    case 1:
        _servo = std::make_shared< ItemRegister >( hal._s1 );
        _servoEnable = std::make_shared< ItemRegister >( hal._s1Enable );
        _servoOverride = std::make_shared< ItemRegister >( hal._s1Override );
        break;

    case 2:
        _servo = std::make_shared< ItemRegister >( hal._s2 );
        _servoEnable = std::make_shared< ItemRegister >( hal._s2Enable );
        _servoOverride = std::make_shared< ItemRegister >( hal._s2Override );
        break;

    case 3:
        _servo = std::make_shared< ItemRegister >( hal._s3 );
        _servoEnable = std::make_shared< ItemRegister >( hal._s3Enable );
        _servoOverride = std::make_shared< ItemRegister >( hal._s3Override );
        break;

    case 4:
        _servo = std::make_shared< ItemRegister >( hal._s4 );
        _servoEnable = std::make_shared< ItemRegister >( hal._s4Enable );
        _servoOverride = std::make_shared< ItemRegister >( hal._s4Override );
        break;

    case 5:
        _servo = std::make_shared< ItemRegister >( hal._s5 );
        _servoEnable = std::make_shared< ItemRegister >( hal._s5Enable );
        _servoOverride = std::make_shared< ItemRegister >( hal._s5Override );
        break;

    case 6:
        _servo = std::make_shared< ItemRegister >( hal._s6 );
        _servoEnable = std::make_shared< ItemRegister >( hal._s6Enable );
        _servoOverride = std::make_shared< ItemRegister >( hal._s6Override );
        break;

    case 7:
        _servo = std::make_shared< ItemRegister >( hal._s7 );
        _servoEnable = std::make_shared< ItemRegister >( hal._s7Enable );
        _servoOverride = std::make_shared< ItemRegister >( hal._s7Override );
        break;

    default:
        qDebug()
            << QTime::currentTime().toString()
            << "Not a valid io number to attach servo.";
        return false;
    }

    _minAngle = min;
    _maxAngle = max;

    _servo->write( min );
    _servoOverride->write( 0x01 );
    _servoEnable->write( 0x03 );

    QThread::msleep( 500 );

    return true;
}

const QString& Servo::name() const
{
    return _name;
}

uint16_t Servo::read()
{
    return _servo->read< uint16_t >();
}

void Servo::write( uint16_t read )
{
    _servo->write( read );
}

void Servo::enable()
{
    _servoEnable->write( 0x03 );
}

void Servo::disable()
{
    _servoEnable->write( 0x00 );
}

bool Servo::isAttached() const
{
    return _servoEnable->read< uint8_t >() == 0x03 ? true : false;
}

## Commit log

2016-10-30 Start work on expansion board
    [expansion_board_V0.sch]
2016-10-30 Add some I/Os connectors
    [expansion_board_V0.sch]
2016-11-13 update fpga project
    [c5_pin_model_dump.txt, hps_sdram_p0_summary.csv]
2016-11-19 Add custom leds project: (A project with a little IP that control leds)
    [c5_pin_model_dump.txt, hps_sdram_p0_summary.csv]
2016-11-20 Start working on Kernel module (simple IO leds module driver)
2016-11-20 Update custom led project
    [boards.cfg, hawkboard-ais-nand.cfg, imximage.cfg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]
2016-11-20 Add files to create a bootable image for the DE0 nano SoC board
2016-12-04 add qei
    [expansion_board_V0.sch]
2016-12-04 hub usb
    [expansion_board_V0.sch]
2016-12-04 Rework hbridge section and add qei
    [expansion_board_V0.sch]
2016-12-04 Add logic level translator, missing I2C and UART
    [expansion_board_V0.sch]
2016-12-04 Add current sense for motor and servo
    [expansion_board_V0.sch]
2016-12-10 Clean motor section: Rework DRV8432 Remove QEI differential as we use cheap sensor Create Power and Analog section [WIP]
    [expansion_board_V0.sch]
2016-12-11 Add isolator + VCC/GND on all I/Os Add WiFi module from Gemicom
    [expansion_board_V0.sch]
2016-12-11 Add FPGA connectors
    [expansion_board_V0.sch]
2016-12-12 modifs schéma en cours
    [expansion_board_V0.sch]
2016-12-16 Remove useless servo
    [expansion_board_V0.sch]
2016-12-17 Elec done. A verifier.
    [Conception.xlsx, expansion_board_V0.sch]
2016-12-18 Add a 3rd UART
    [Conception.xlsx, expansion_board_V0.sch]
2017-01-08 wip power & motor
    [expansion_board_V0.brd]
2017-01-09 WIP placement
    [expansion_board_V0.brd]
2017-01-18 en cours de routage. footprint wifi et arduino à revoir corrections sch - connecteur fpga : power pins - montage aop pour adc - inversion pin io drivers pour faciliter le routage brd : - inversion co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
    [expansion_board_V0.brd, expansion_board_V0.sch]
2017-01-19 Add adafruit library for Arduino connector and update it
    [expansion_board_V0.brd, expansion_board_V0.sch]
2017-01-19 Add Gemicom lib + update module in sch/brd
    [expansion_board_V0.brd, expansion_board_V0.sch]
2017-01-21 Update connector placement fo match Nano SOC board
    [expansion_board_V0.brd]
2017-01-23 Update WPS and LED on WiFi module
    [expansion_board_V0.brd, expansion_board_V0.sch]
2017-01-29 Routage ok
    [expansion_board_V0.brd, expansion_board_V0.sch]
2017-01-31 Add stm32f4xx library
2017-01-31 [WIP] Add IMU based on stm32f4 and Invsense all-in-one
    [expansion_board_V0.brd, expansion_board_V0.sch]
2017-02-04 PCB envoyé chez eurocircuit
    [Conception.xlsx, expansion_board_V0 - Pannel.brd, expansion_board_V0.brd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]
2017-02-05 Derniere modif elec
    [FPGA board - dimensions.SLDPRT, expansion_board_V0 - Pannel.brd, expansion_board_V0.brd]
2017-02-05 Pb DRC sur l'imu
    [expansion_board_V0 - Pannel.brd]
2017-02-05 Update schematics with new library
    [expansion_board_V0.brd, expansion_board_V0.sch]
2017-02-05 IMU footprint ok Elec posté sur Eurocircuit
    [expansion_board_V0 - Pannel.brd, expansion_board_V0.brd, expansion_board_V0.sch]
2017-02-08 Add drivers
2017-02-08 Update driver
2017-02-11 Working and final distrib (zImage, drivers, scripts)
2017-02-12 Add cpp project of custom led
2017-02-12 Add memory manager to motor module
2017-02-12 Add Pid filters and polar to wheels convertion class
2017-02-18 [HPS_FPGA_LED] move from verilog to VHDL, add pwm core and add project SDC for clock constraints
2017-02-18 Add Qt project to control leds
2017-02-19 modify IOs to connect to the real daugther board
2017-02-22 Ajout de commentaires bug carte électronique sur le schéma
    [BOM.xlsx, Conception.xlsx, expansion_board_V0.brd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]
2017-02-25 modify pinout to be compatible with new h bridge reset/fault pins arrangments, instantiate 2 RV systems as PI controller
    [stp_debug2.stp]
2017-02-28 Add datasheet capteur couleur
    [Grove - I2C Color sensor v1.2.brd, Grove - I2C Color sensor v1.2.sch, expansion_board_V0.brd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]
2017-03-03 Add simu feedforward motor
2017-03-06 new system using updated HPS access to robot, through the use of large pio_n
    [stp_debug2.stp]
2017-03-06 add pkg files, rename hps_0 into hps_arm, add sopcinfo file and generated .h file to be integrated into ARM layer
2017-03-07 implement first version of layer 1, still missing IO management, H Bridge fault, and Servo current (missing ADC)
2017-03-07 add debounce core to filter input pins and connect it to MM
2017-03-17 fix reset issue and enabled for esc
2017-03-19 add first layer 2 implementation for odometry
2017-03-19 Validate layer 2: position and motor control
2017-03-20 Add some documentation. Add common file. Rework some includes
    [main.cpp]
2017-03-20 Handle case where the io is unused
2017-03-24 reduced size orca, add carrousel qei and pid
2017-03-28 WIP: Rework main and archi
    [main.cpp]
2017-04-06 Some cleanup and fix the state machine for hard stop
    [main.cpp]
2017-04-11 Fix SIMU mode and carrousel is working
    [main.cpp]
2017-04-18 elec ok
    [Conception.xlsx, expansion_board_V0.brd, expansion_board_V0.sch]
2017-04-20 bug fix on low frequencies for pwm, connect uart and i2c, rework io mapping
2017-04-22 Fix button handling
2017-04-22 Working carrousel setPosition. Fix position function. Example for carrousel module
    [main.cpp]
2017-04-22 Add servo module
2017-04-23 Move servo defines in header file. Add pid registers init in system manager
2017-04-23 Fix trajectory manager init. Add saturation for pid in system manager
    [main.cpp]
2017-05-01 3rdparty shared library for DE0 board
2017-05-07 Start working on strat. Remove action flow in system state machine.
2017-05-13 Add RPLidar dependency. Fix systemManager. Wip trajectory manager
    [main.cpp]
2017-05-14 Fix system manager PID section. Fix state machine
    [main.cpp]
2017-05-14 Fix trajectory manager module: Properly handle hardstop button
2017-05-15 add calibration project and matlab frame parsing
    [Configuration.h]
2017-05-16 Add color sensor module
2017-05-16 Update Color sensor module
2017-05-16 Add support for color led and start color sensor integration to system module
2017-05-16 Fix color sensor
2017-05-17 add system ll in layer 1 to handle i2c sensors (color & distance)
2017-05-19 Some fixes. Add turbine esc module
    [main.cpp]
2017-05-19 Blink color led when game start
2017-05-20 Eject cylinder ok
2017-05-21 Rework init sequence to be safe
    [ColorSensor.cpp, main.cpp]
2017-05-22 Big big rework of all actions
    [MoveArmsAction.cpp]
2017-05-22 WIP: add algo to find matching color on a multi-color cylinder
2017-05-23 Add new register for motor orientation and add the ref in color sensor module
2017-05-23 Add support for unblock servo to do the fusees
2017-05-23 Fix color sensor module and rework system manager
    [ColorSensor.cpp, MoveArmsAction.cpp, Servo.hpp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]
2017-05-23 Clean reset sequence. Update sensor module with init and isEmpty methods.
    [ColorSensor.cpp]
2017-05-23 Fix servo: All arms actions are tested and valid
    [MoveArmsAction.cpp, Servo.hpp]
2017-05-23 Fix init sequence for color target. Remove action in yellow sequence
    [ColorSensor.cpp]
2017-05-24 Fix color sensor check function
    [ColorSensor.cpp]
2017-05-25 WIP strat blue opti timing and fix funny action
    [ColorSensor.cpp, MoveArmsAction.cpp]
2017-05-25 Remove eigen. Add pusher servo support. Sequence updated (shortest way)
    [ColorSensor.cpp, MoveArmsAction.cpp, Servo.hpp]
2017-05-26 Update esc config
2017-05-26 Fix colorSensor looping indefinitly
    [ColorSensor.cpp]
2017-05-26 Fix timer 90s event handling
2017-05-26 Arret urgence moved to Thread
2017-05-27 Add release file for match 4 in case of...
2017-06-04 Add pid plot
2017-06-04 Ajout pièce lors de la coupe
    [01 Table.SLDPRT, 02 Fusée.SLDPRT, 03 Bascule.SLDPRT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]
2019-01-19 add DE10 pinout as a second device for quartus project
2019-01-22 add 6 UARTs to communicate between ARM & FPGA, add Makefile from GHRD to be able to generate dts & dtb files. hps_common_board_info & hps_fpga_board_info come from DE10 GHRD, because the ones from th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

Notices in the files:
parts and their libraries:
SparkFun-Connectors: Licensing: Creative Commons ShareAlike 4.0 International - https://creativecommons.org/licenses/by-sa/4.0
